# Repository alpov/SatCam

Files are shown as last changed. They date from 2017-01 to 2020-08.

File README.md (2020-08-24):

# PSAT-2 PSK/SSTV transponder

This repository hosts public parts of two boards from [PSAT2](http://www.aprs.org/psat2.html), a 1.5U CubeSat by US Naval Academy. These boards were developed at Dept. of Radio Electronics, Brno University of Technology, Czech Republic. The source files do not include authorization codes for SSTV and uplink commanding for PSK transponder.

**PSK transponder board** is an updated version of the PSK transponder with beacon and telemetry, used on [PSAT](http://www.aprs.org/psat.html) and [BRICSAT-1](http://www.aprs.org/bricsat-1.html). Transponder documentation available for [PSAT](http://www.urel.feec.vutbr.cz/esl/files/Projects/PSAT/P%20sat%20transponder%20WEB%20spec02.htm) and [BRICSAT-1](http://www.urel.feec.vutbr.cz/esl/files/Projects/BRICsat/Bricsat%20transponder%20WEB%20spec02.htm).

**SSTV transmitter board** provides a Slow-scan Television (SSTV) signal generator with PSK/CW telemetry, APRS uplink, and camera module. It is based on STM32F446RET6 microcontroller. Supported SSTV modes are Robot36, Robot72, MP73 and MP115.

## Important information (UPDATED Aug 2020)

* Current PSAT2 status
  * SSTV 70cm operational, images in Flash occasionally updated (thanks to PY5LF, OK2PNQ, OK5MP)
  * PSK 10m=>70cm transponder operational, mode A, open for users
  * APRS 2m is down (transmitter failure) => user SSTV commanding is not possible

* Please **send your SSTV images** to alpov@alpov.net. I am collecting the emails from reporters and occasionaly send them some news. Other info source is [AMSAT-BB](https://www.amsat.org/pipermail/amsat-bb/).
  * [Gallery of decoded SSTV images](http://www.urel.feec.vutbr.cz/esl/psat2/sstv/).
  * [Online telemetry decoder](http://www.urel.feec.vutbr.cz/esl/psat2/psat2tlm.php) - please use for PSK-31 telemetry upload.
  * [Decoded telemetry of PSK and SSTV boards](https://docs.google.com/spreadsheets/d/1X_4X0AgCshNDFIrDecOif41eRRwNzOKZwRn9tjI5_hs/edit?usp=sharing).
  * [SatNOGS for PSAT2](https://network.satnogs.org/observations/?future=0&good=1&bad=0&unvetted=0&failed=0&norad=44354).

* [Description of overlays](Docs/Overlay.md) in camera images.

* [Standalone camera design](Docs/SatCam.md) (for cancelled [PSAT3](http://www.aprs.org/psat3.html), [operations](Docs/PSAT3-operations.md)).

* [PocketQube camera design](Eagle/satcam_v4B_pocket_pcb_inside.pdf) (for [HADES](https://www.ure.es/camara-sstv-de-la-universidad-de-brno-para-el-satelite-hades-de-amsat-ea/) satellite).

## Transponder modes overview
The main function of the transponder is to receive PSK signals from 29.48 MHz uplink (passband from 29.4804 to 29.4826 MHz) and transmit them as a FM signal at 435.350 MHz downlink. The downlink is mixed with telemetry streams and SSTV images.

The PSK board switches between modes A to D according to available power. Battery voltage is checked periodically and after each transmitted character. If it crosses a boundary, the mode is switched. Moreover, if the voltage falls below a critical limit, the transmission is stopped immediately. This behavior can be observed in mode D, when only a part of the telemetry is transmitted.

All operations are limited to Sun detection, which is controlled by SUNWIRE signal. The SUNWIRE is fail-safe checked by state machine. After MCU reboot, the Sun signal is always high. It goes low after falling edge on SUNWIRE. If the SUNWIRE is low for more than 30 minutes, it is set to high automatically, otherwise with rising edge on SUNWIRE. Interconnects between both boards and PSAT-2 are shown [in a block diagram](Docs/psk_sstv_interconnect.png).

Communication is divided into 20sec time slots. There are 6 slots for modes A/B/C, and 9 slots for mode D. The telemetry is transmitted in every 1st slot or if PSK uplink is detected. Additionally, an SSTV image or telemetry is added to the transmitted signal. The time slots do not affect the PSK transponder function, so there is no need to fit with the PSK uplink signal into a time window. However, advanced functions such as commanding, telemetry and SSTV, are synchronized into these windows.

Users will be able to command these functions after the system has been successfully activated in space and we have completed successful checkout.

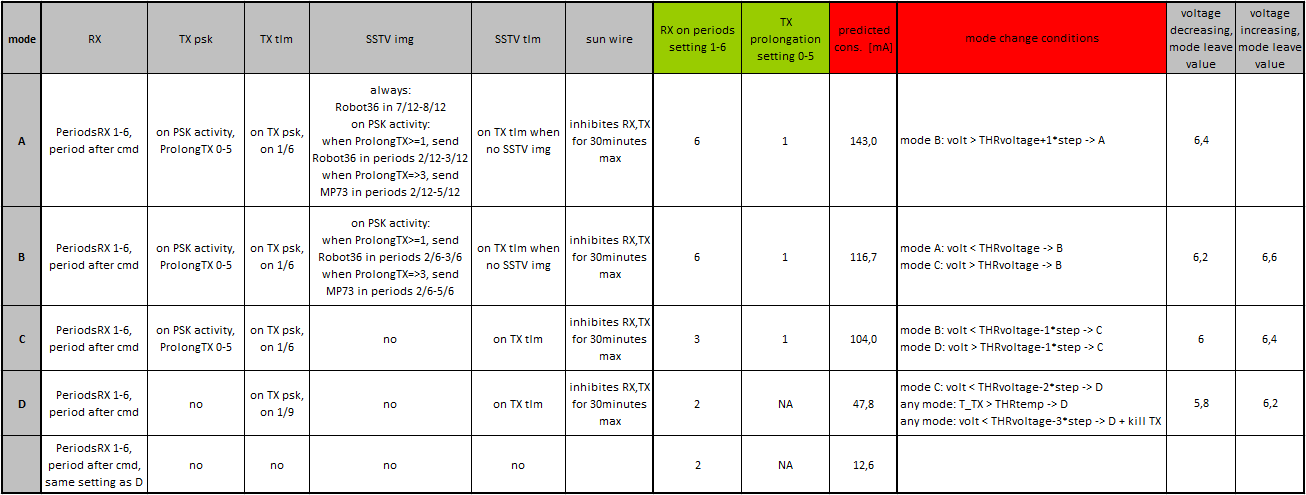
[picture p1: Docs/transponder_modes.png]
Transponder modes


## Telemetry streams
The PSK MCU generates telemetry data in PSK31 format, which is transmitted on 435.350 MHz, carrier at 374 Hz. This telemetry consists of current and historical frame. Current frame contains frame counter, reboot counter, values of PSK level, AGC, battery voltage, 5V voltage, current, RX temperature, and several period counter values. History frame is pseudo-randomly selected from memory and contains the same information except for period counters. Example telemetry frame: *PSAT-2 C apng eFaaijtkpokoaB aaaa A aokF eEadjluappjxay*. Such frame can be [decoded with the provided PHP decoder](http://www.urel.feec.vutbr.cz/esl/psat2/psat2tlm.php). Valid telemetry frames are automatically saved for further analysis.

The other telemetry stream is generated by SSTV MCU, transmitted in PSK31 format on the same frequency, carrier at 280 Hz. Telemetry contains current state of non-persistent tick counter, measurements of MCU temperature and ambient light in lux, state of several counters (authorization, planned events, reboots, errors, audio starts, camera images, commands accepted, commands rejected, commands unauthorized). Example telemetry frame: *PSAT-2 S ashd aDbiaaaa qralaitkboFxaa*. Again, such frame can be [decoded with the provided PHP decoder](http://www.urel.feec.vutbr.cz/esl/psat2/psat2tlm.php).

## SSTV operation
SSTV MCU can be commanded through APRS commands. If no command is received during 60 seconds, it starts *auto* mode. In this mode, all transmissions are synchronized to PSK TX. SSTV board can transmit PSK telemetry or SSTV images in Robot36 and MP73 modes. Images are progressively selected alternately from ROM and FLASH. ROM images are hard-coded to firmware, while FLASH images are grabbed from on-board camera. After each reboot, first 8 images in FLASH are taken with 30sec separation.

APRS commands addressed to special callsign will change the mode to *manual*. Details on public commanding will be added after successful deployment and initial testing of the satellite.

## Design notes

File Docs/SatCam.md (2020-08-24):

# SatCam - SSTV encoder for OV2640

SatCam in an SSTV encoder with OV2640 camera. It is based on STM32F446RET6 microcontroller. Supported SSTV modes are Robot36, Robot72, MP73 and MP115. SatCam was originally developed as a part of PSAT2 satellite project and later redesigned as a stand-alone module.

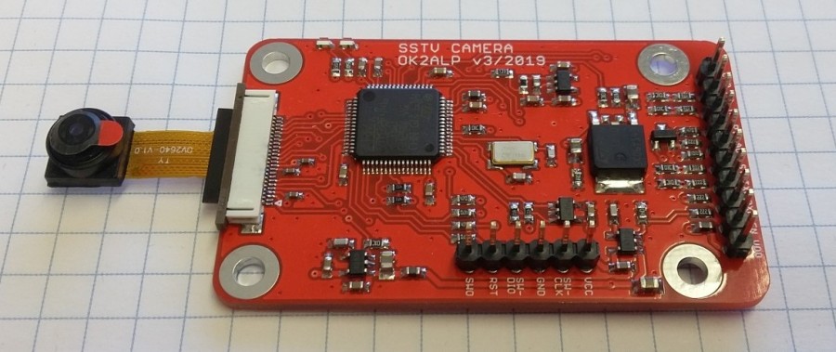
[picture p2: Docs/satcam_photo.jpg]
SatCam prototype photo


[SatCam schematic](../Eagle/satcam_v3_mini_sch.pdf) - [SatCam PCB](../Eagle/satcam_v3_mini_tvalues.pdf)

SatCam can be commanded from e.g. an APRS link, the UART works at 9600 8N1. It looks for `SATCAMERA:` keyword, followed by a command, case insensitive. End of line is `<CR>`, `<LF>` or `{`. Empty lines and messages without proper keyword are ignored. All commands including the keyword are case insensitive. Example: `SatCamera:sstv.live.73<CR>`.

Another way of using SatCam is to setup its initial configuration with UART and then use its input signals only.

## Pin connections
| Pin | Description |
| ----- | --- |
| `M0`  | mode select (0-3)
| `M1`  | mode select (0-3)
| `PTT` | open-drain PTT output, active low during TX
| `AUD` | audio output
| `ST`  | start trigger input
| `RXD` | UART input
| `TXD` | UART output
| `EN`  | voltage regulator enable input
| `VDD` | power supply

Silkscreen of `RXD` and `TXD` is mixed up on the 1st PCB revision. Current schematic and PCB use the ordinary meaning (RXD is the input to SatCam, TXD it the output).

## Voltage levels
| Pin | Levels |
| ----- | --- |
| `ST`, `M0`, `M1`  | 5V (can be changed with R7, R8, R9)
| `TXD`, `RXD` | 3V3 (RXD can be changed with R4, TXD needs level converter)
| `EN` | >2.3V enabled, <0.5V or open disabled
| `PTT` | open-drain, max. 25V
| `AUD` | default SSTV audio is 1.5Vpp to high impedance (>5kohm) load
| `VDD` | 3.2-16V (3.1-6V if R31=0ohm, IC6 not placed)

## Current consumption
| Mode | Avg. current |
| --- | --- |
| disabled with EN input | 0.6mA
| idle, monitoring UART | 2.8mA
| taking picture, ~1.3 seconds before each image | 60.6mA
| transmitting audio, with short peaks | 10.3mA

## Tested OV2640 modules
* [AdvancedTech](https://www.aliexpress.com/item/32898143505.html): landscape, FOV ~50°, [example](ov2640_AdvancedTech.jpg)
* [Your Cee Mini](https://www.aliexpress.com/item/33058626691.html): landscape, FOV ~60°, [example](ov2640_YourCeeMini.jpg)
* [Your Cee Wide](https://www.aliexpress.com/item/33058626691.html): landscape, FOV ~120°, [example](ov2640_YourCeeWide.jpg)
* [Alice1101983](https://www.aliexpress.com/item/32978120017.html), [ModuleFans](https://www.aliexpress.com/item/33042725935.html): portrait, [example](ov2640_Alice.jpg)

## SatCam commands

The module monitors RXD line when idle and looks for `SATCAMERA:` identifier. Expected commands are for SSTV, PSK and CW systems. Other commands (CAMCFG and DEBUG) are protected by a PIN. User PIN can be set to a custom number, master PIN is fixed for the particular module (computed from the MCU unique ID). It is possible to send protected commands for the next 15 minutes after the AUTH command with a correct PIN. Master PIN can be read using `psk.nvinfo` and `debug.status` commands in case when the user PIN is not set (i.e. is zero).

| Command syntax | Example | Parameters |
| --- | --- | --- |
| `sstv.live.MODE.OVERLAY` | `sstv.live.36` (send picture as Robot36) | MODE is `36` for Robot36, `72` for Robot72, `73` for MP73, `115` for MP115 (default: 36)
| `sstv.rom.MODE.PAGE_NUMBER.OVERLAY` | `sstv.rom.115.3.hello` (send hardcoded image 3 as MP115, with overlay) | PAGE_NUMBER is ROM memory page (default: 0), OVERLAY is user-defined text, `.` and `{` not allowed, up to 13 chars (default: none)
| `psk.MESSAGE.SPEED.FREQ` | `psk.hello.31.1000` (send message as PSK-31 at 1kHz) | MESSAGE is either user-defined text (`.` and `{` not allowed) or `nvinfo` or `config`
| `psk.config.SPEED.FREQ` | `psk.config.125.1000` (send configuration as PSK-125 at 1kHz) | SPEED is `31`, `63`, `125`, `250`, `500`, `1000` (default: 31, for config/nvinfo: 125)
| `psk.nvinfo.SPEED.FREQ` | `psk.nvinfo.125.1000` (send NVinfo log as PSK-125 at 1kHz) | FREQ is 100-7000Hz (default: 800)
| `cw.MESSAGE.WPM.FREQ` | `cw.hello.25.1000` (send message as 25WPM CW at 1kHz) | WPM is word per minute speed (5 to 40)
| `auth.PIN` | `auth.1234` (authorize with PIN 1234) | PIN is user or master access code

| Command syntax | Default | Description |
| --- | --- | --- |
| `camcfg.delay.DELAY` | 1000 | Camera module initial delay. DELAY is 100-5000ms.
| `camcfg.qs.QS` | 5 | JPEG quality factor. QS is 0-255.
| `camcfg.agc.ceiling.AGC_CEILING` | 16 | Automatic gain control. AGC_CEILING is 2, 4, 8, 16, 32, 64, 128.
| `camcfg.agc.manual.AGC_VALUE` | 0 | Manual gain control. AGC_MANUAL is 0-1023.
| `camcfg.aec.auto` | | Automatic exposure control.
| `camcfg.aec.manual.AEC_VALUE` | `auto` | Manual exposure time. AEC is 0-65535 or `auto`.
| `camcfg.awb.AWB_TYPE` | `sunny` | Automatic white balabce. AWB is `auto`, `sunny`, `cloudy`, `office`, `home`.
| `camcfg.rotate.ROTATE` | off | Camera rotation (upside down). ROTATE is `off` or `on`.
| `camcfg.start.0.COMMAND` | `SSTV.LIVE.36` | Command for M0=0, M1=0.
| `camcfg.start.1.COMMAND` | `SSTV.LIVE.73` | Command for M0=1, M1=0.
| `camcfg.start.2.COMMAND` | `PSK.NVINFO.125.1000` | Command for M0=0, M1=1.
| `camcfg.start.3.COMMAND` | `SSTV.ROM.115.0` | Command for M0=1, M1=1.
| `camcfg.startedge.EDGE_VALUE` | `any` | Active edge for ST trigger input. EDGE_VALUE is `none`, `rising`, `falling` or `any`.
| `camcfg.holdoff.HOLDOFF_TIME` | 2 | Hold-off time after command before next edge detection start. HOLDOFF_TIME is 0-65535sec.
| `camcfg.callsign.CALLSIGN` | `SatCam` | Module callsign, for SSTV overlay and PSK/CW messages.
| `camcfg.autoreboot.REBOOT_TIME` | 0 | Periodic reboot. REBOOT_TIME is 0 or >=120sec. Careful when uptime>autoreboot, camera will reboot immediately without saving the value.
| `camcfg.userpin.PIN` | 0 | Set user PIN for `camcfg` and `debug` commands.
| `camcfg.clearlog` | | Clear EEPROM logs.
| `camcfg.reboot` | | Safe MCU reboot (with NVIC).
| `camcfg.load` | | Load configuration from EEPROM (always after power-up).
| `camcfg.save` | | Save current configuration to EEPROM.
| `camcfg.default` | | Load default SatCam configuration.

| Command syntax | Description |
| --- | --- |
| `debug.status` | Write status (configuration and NVinfo) to terminal.
| `debug.reset.RESET_TYPE` | Debug MCU reset. RESET_TYPE is `nvic`, `watchdog`, `fault`.
| `debug.sendjpeg` | Send JPEG from camera to terminal.
| `debug.eeprom.fullerase` | Perform full EEPROM erase (configuration and logs).
| `debug.eeprom.dump` | Dump configuration EEPROM page to terminal.
| `debug.adc.voltage` | Measure VDD voltage and write to terminal.
| `debug.adc.temp` | Measure core temperature and write to terminal.

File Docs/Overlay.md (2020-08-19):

## Live image from camera
`PSAT-2 +69605 8°C #062 89lx1`
* `+69605` timestamp - minutes elapsed since reboot
* `8°C` MCU temperature when taking the image
* `#062` counter of camera snapshots
* `89lx1` light when taking the image, mantisa and exponent in lux, i.e. 89*10^1 = 890lux
* Timestamp, temperature and light are actual.
* Note: Light exposition seems to be too low - sensor was probably misplaced during satellite integration.

## Image from Flash memory
`PSAT-2 +24940 11°C #047 17lx3 F#13`
* Timestamp, temperature and light are from the moment of shooting.
* `F#13` is position no. 13

## Image from ROM memory
`PSAT-2 +26148 16°C ROM #10`
* Timestamp and temperature are actual.
* `ROM #10` is position no. 10.

## Thumbnail image from all Flash memories
`PSAT-2 +29312 13°C thumbnails`
* Timestamp and temperature are actual.

## Camera information
`11520B g256 e9`
* `11520B` - size of original JPEG snapshot
* `g256` - camera gain (AGC)
* `e9` - camera exposure (AEC)

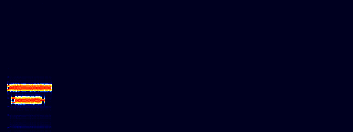
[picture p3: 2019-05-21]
Docs/modeC_no_PSK.PNG

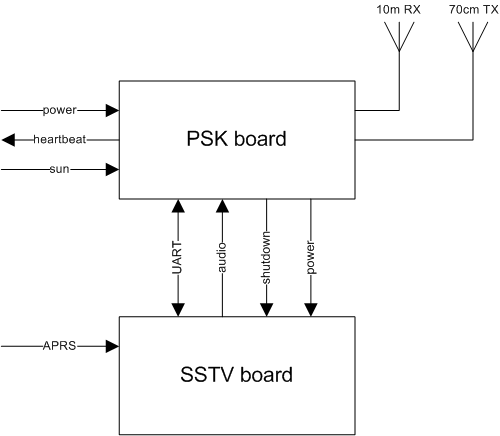
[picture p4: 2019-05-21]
Docs/psk_sstv_interconnect.png

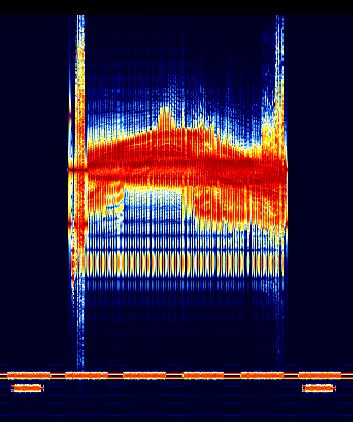
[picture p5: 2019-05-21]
Docs/modeB_with_PSK_TXprolong3.PNG

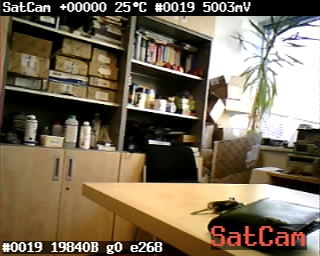
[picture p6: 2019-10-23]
Docs/ov2640_YourCeeMini.jpg

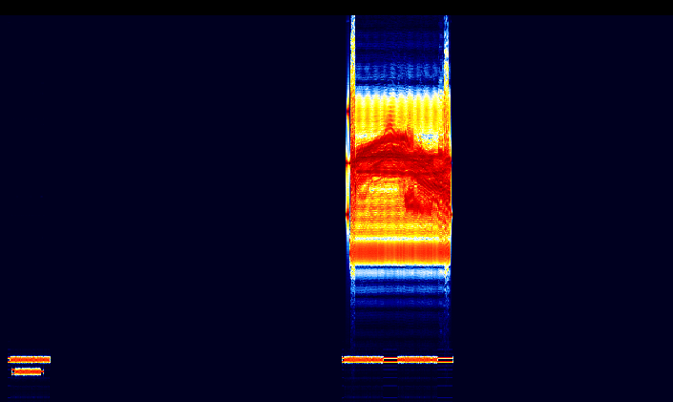
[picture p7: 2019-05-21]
Docs/modeA_no_PSK.PNG

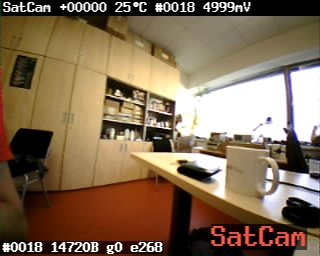
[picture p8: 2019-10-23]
Docs/ov2640_YourCeeWide.jpg

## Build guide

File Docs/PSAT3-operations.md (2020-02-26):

# SSTV camera on PSAT3

SatCam is an [SSTV encoder with OV2640 camera](SatCam.md). It is based on STM32F446RET6 microcontroller. Supported SSTV modes are Robot36, Robot72, MP73 and MP115. SatCam was originally developed as a part of PSAT2 satellite project and later redesigned as a stand-alone module.

When enabled, camera **sends a live picture** in Robot36 or MP73 **every 10 minutes**. The SSTV transmission always come after APRS.

## Current status

* Current PSAT3 status: **waiting for deploy**

* Gallery of SSTV images - TBD. SatNOGS for PSAT3 - TBD. Please send your SSTV images and received runtime status (NVinfo) to alpov@alpov.net.

## SatCam commanding

SatCam can be commanded from the APRS link. It looks for `SATCAMERA:` keyword, followed by a command, case insensitive. Every HAM is allowed to use the following camera commands when the system is enabled.

| Command syntax | Parameters |
| --- | --- |
| `satcamera:sstv.live.MODE.OVERLAY` | MODE is `36` for Robot36, `72` for Robot72, `73` for MP73, `115` for MP115 (default: 36), OVERLAY is user-defined text, `.` and `{` not allowed, up to 13 chars (default: none)
| `satcamera:psk.MESSAGE.SPEED.FREQ` | MESSAGE is either user-defined text (`.` and `{` not allowed) or `nvinfo` or `config`, SPEED is `31`, `63`, `125`, `250`, `500`, `1000` (default: 31, for config/nvinfo: 125), FREQ is 100-7000Hz (default: 800)
| `satcamera:cw.MESSAGE.WPM.FREQ` | MESSAGE is either user-defined text (`.` and `{` not allowed), WPM is word per minute speed (5 to 40), FREQ is 100-7000Hz (default: 800)

| Command examples | Description |
| --- | --- |
| `satcamera:sstv.live` | Send live picture in Robot36
| `satcamera:sstv.live.73` | Send live picture in MP73
| `satcamera:sstv.live.115.de OK2ALP` | Send live picture in MP115, add overlay to image
| `satcamera:psk.hello from space` | Send message `PSAT3 hello from space` in PSK-31 at 800Hz carrier
| `satcamera:psk.config` | Send camera configuration in PSK-125 @ 800Hz
| `satcamera:psk.nvinfo` | Send camera runtime status in PSK-125 @ 800Hz
| `satcamera:cw` | Send a welcome message `73 DE PSAT3 PSAT3 PSAT3 K` at 25WPM @ 800Hz
| `satcamera:cw.morse forever.18` | Send message `PSAT3 morse forever` at 18WPM @ 800Hz

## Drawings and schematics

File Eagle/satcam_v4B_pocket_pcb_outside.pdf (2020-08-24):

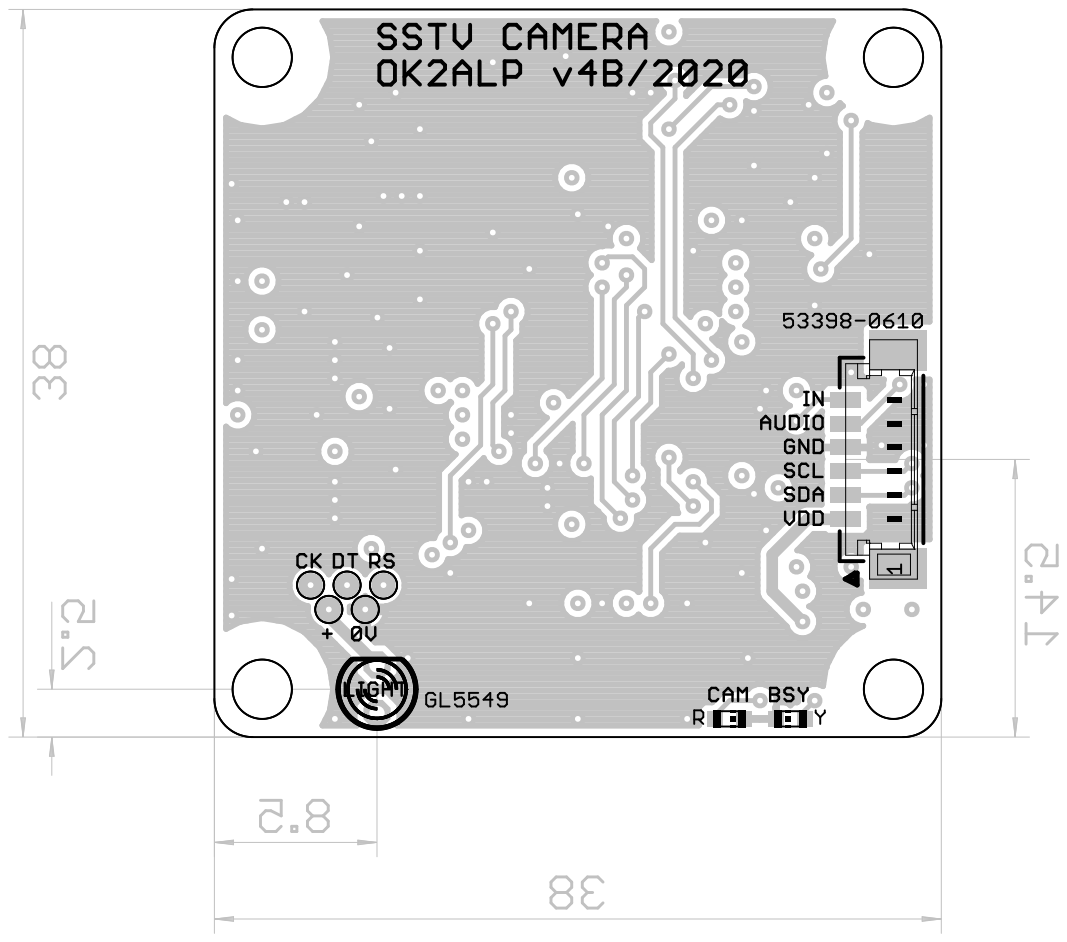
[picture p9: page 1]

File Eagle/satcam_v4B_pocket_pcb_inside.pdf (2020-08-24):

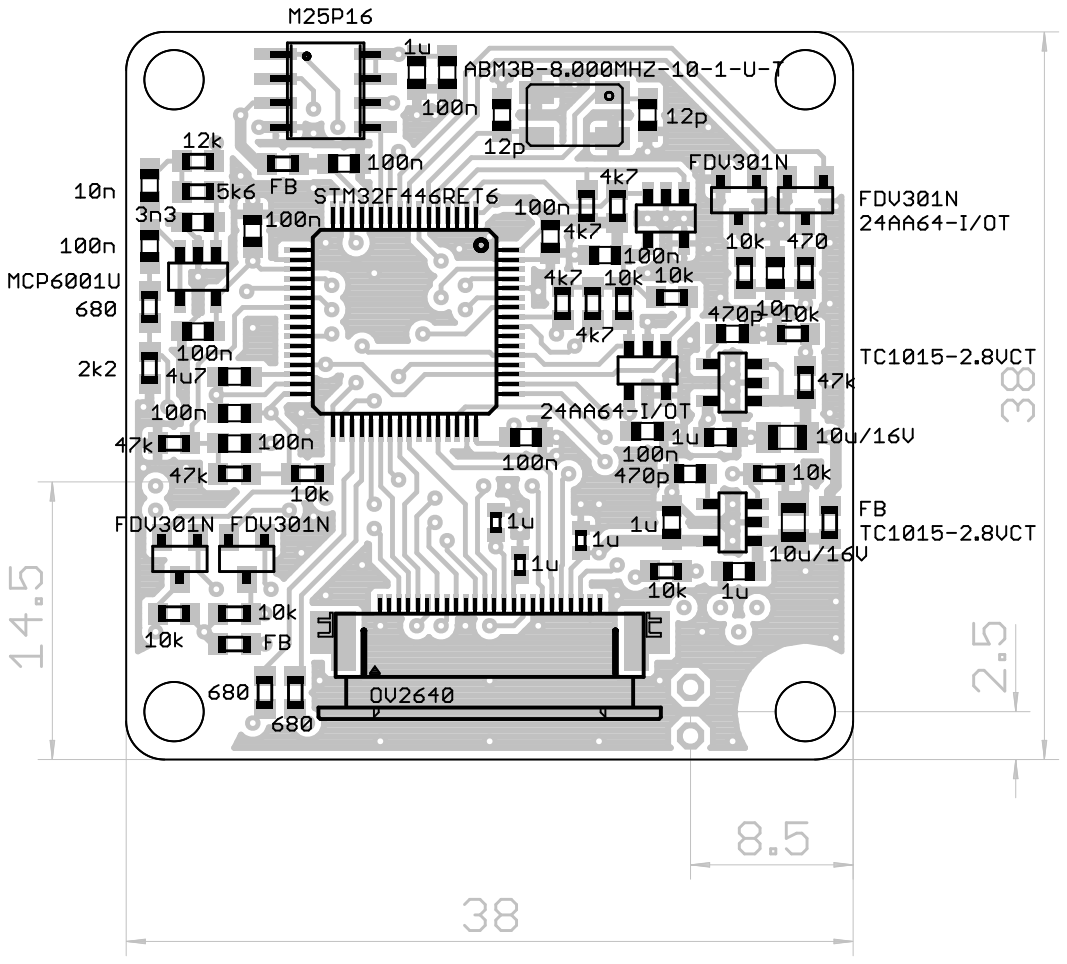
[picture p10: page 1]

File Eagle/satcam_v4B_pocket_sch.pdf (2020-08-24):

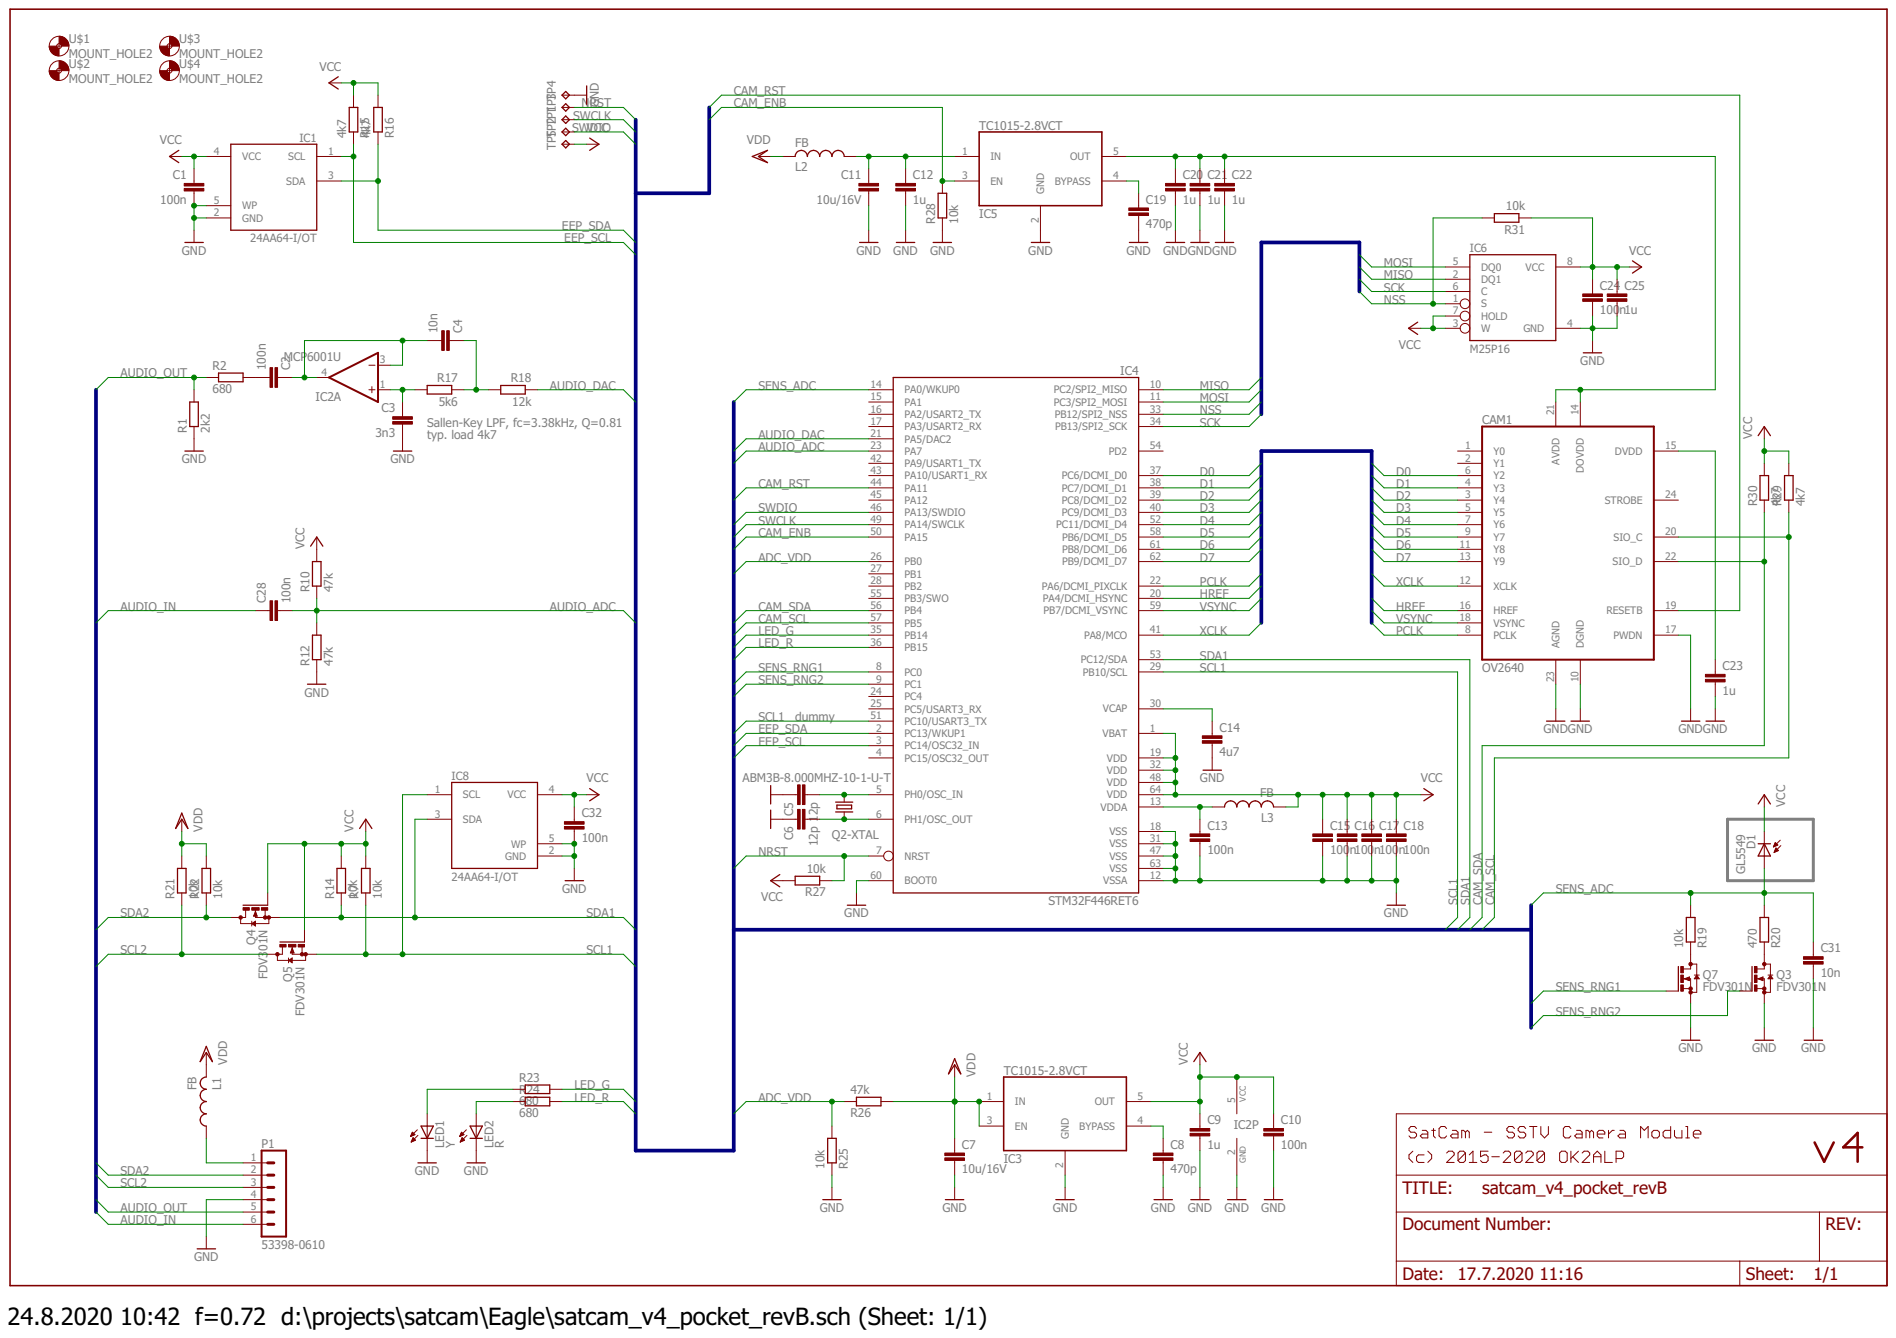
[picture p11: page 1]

Sallen-Key LPF, fc=3.38kHz, Q=0.81
typ. load 4k7

20 SIO_D

22 RESETB

REV: TITLE: Document Number: satcam_v4_pocket_revB

Date: 17.7.2020 11:16 | Sheet: 1/1

24.8.2020 10:42 f=0.72 d:\projects\satcam\Eagle\satcam_v4_pocket_revB.sch (Sheet: 1/1)

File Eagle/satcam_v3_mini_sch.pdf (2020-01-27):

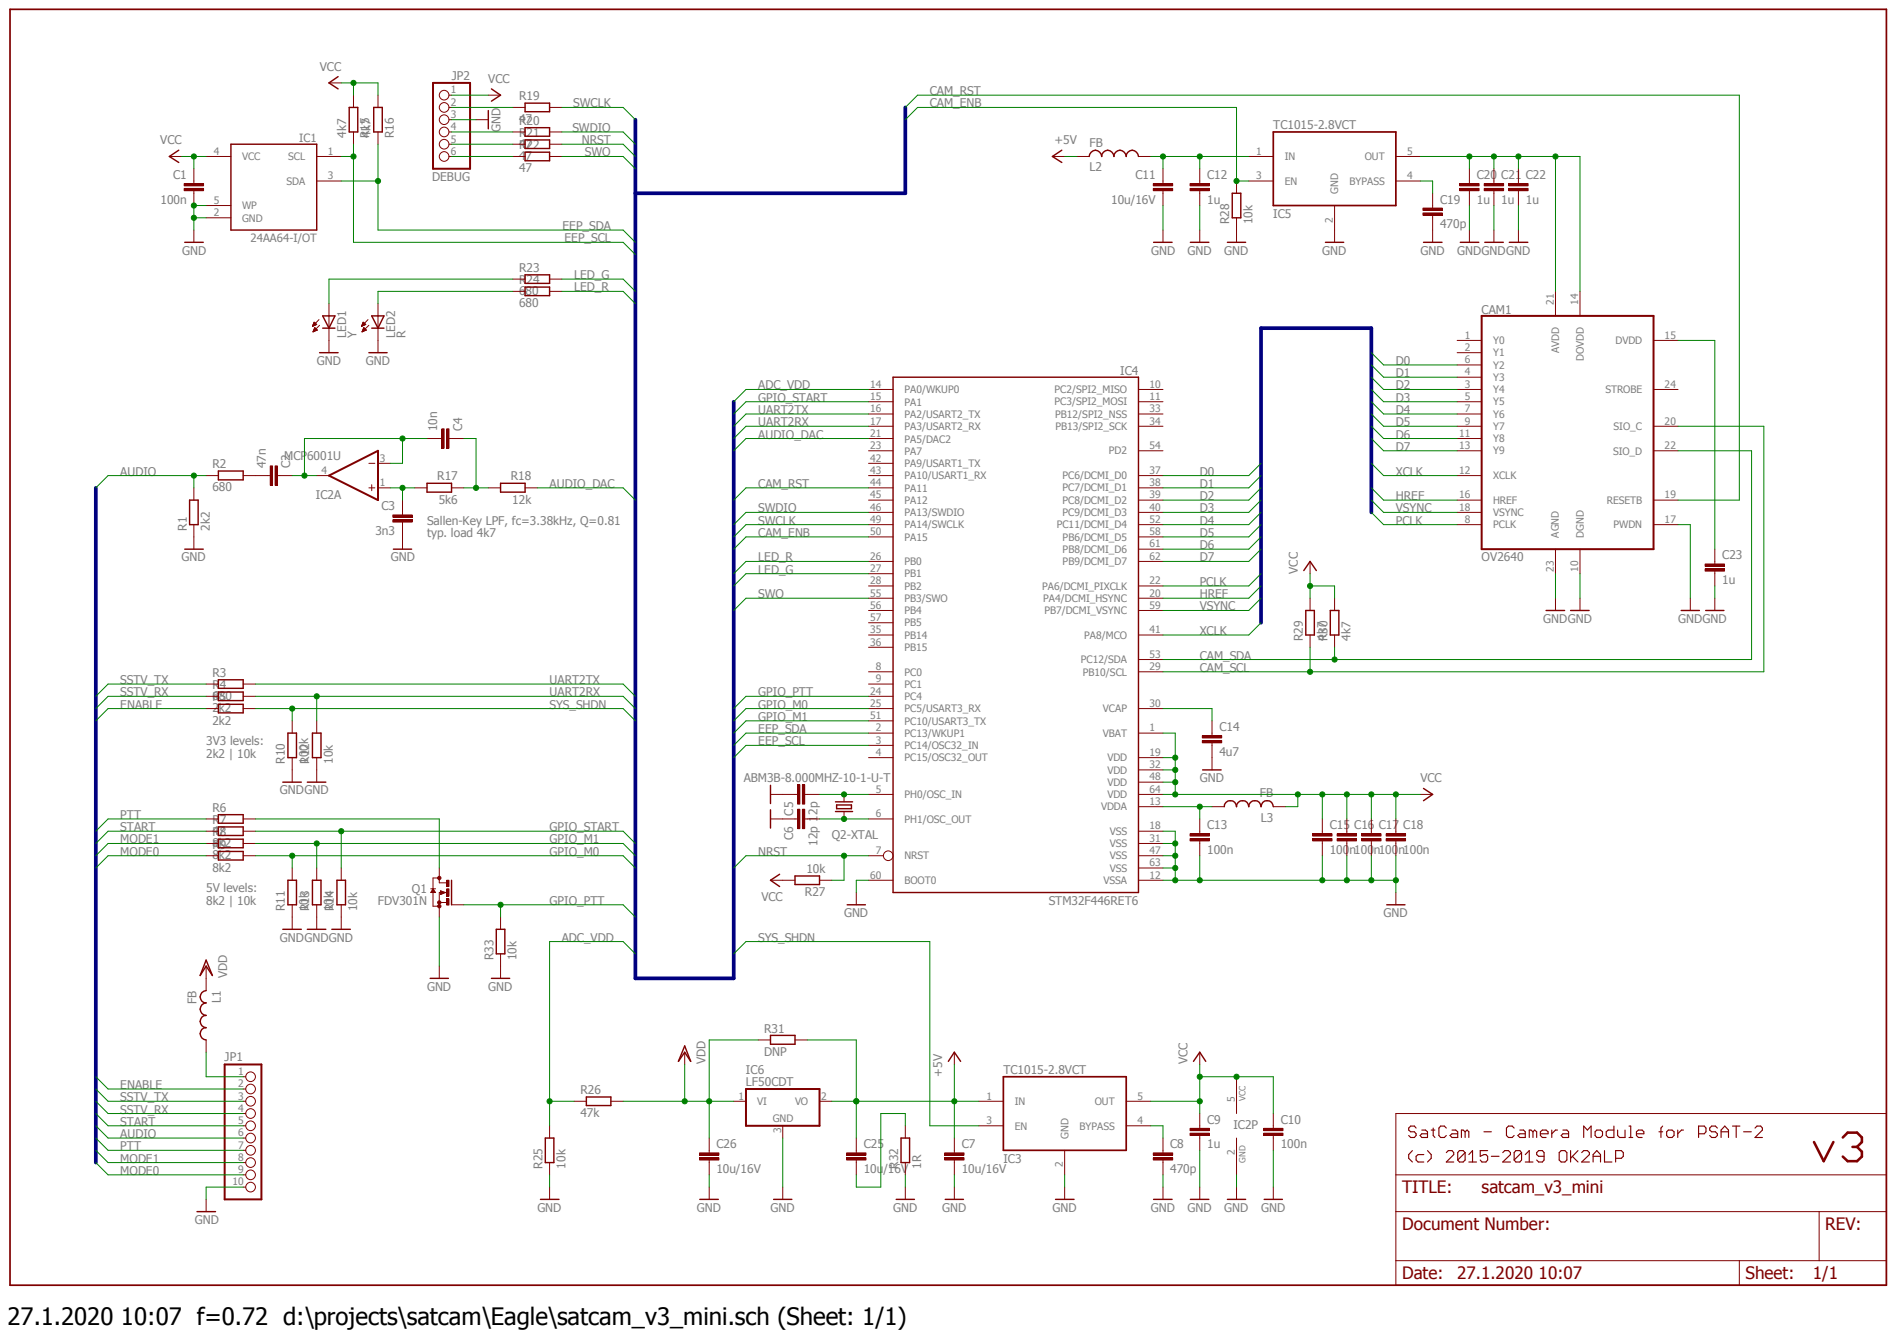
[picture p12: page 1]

Sallen-Key LPF, fc=3.38kHz, Q=0.81
typ. load 4k7

Document Number: | REV:

Date: 27.1.2020 10:07 | Sheet: 1/1

27.1.2020 10:07 f=0.72 d:\projects\satcam\Eagle\satcam_v3_mini.sch (Sheet: 1/1)

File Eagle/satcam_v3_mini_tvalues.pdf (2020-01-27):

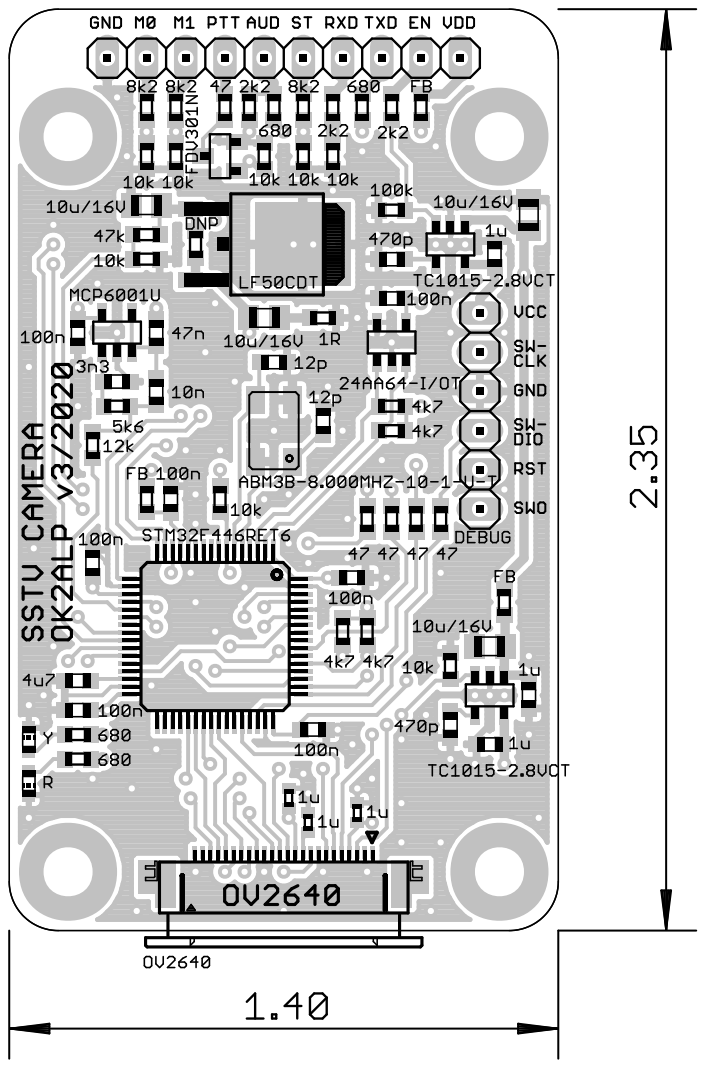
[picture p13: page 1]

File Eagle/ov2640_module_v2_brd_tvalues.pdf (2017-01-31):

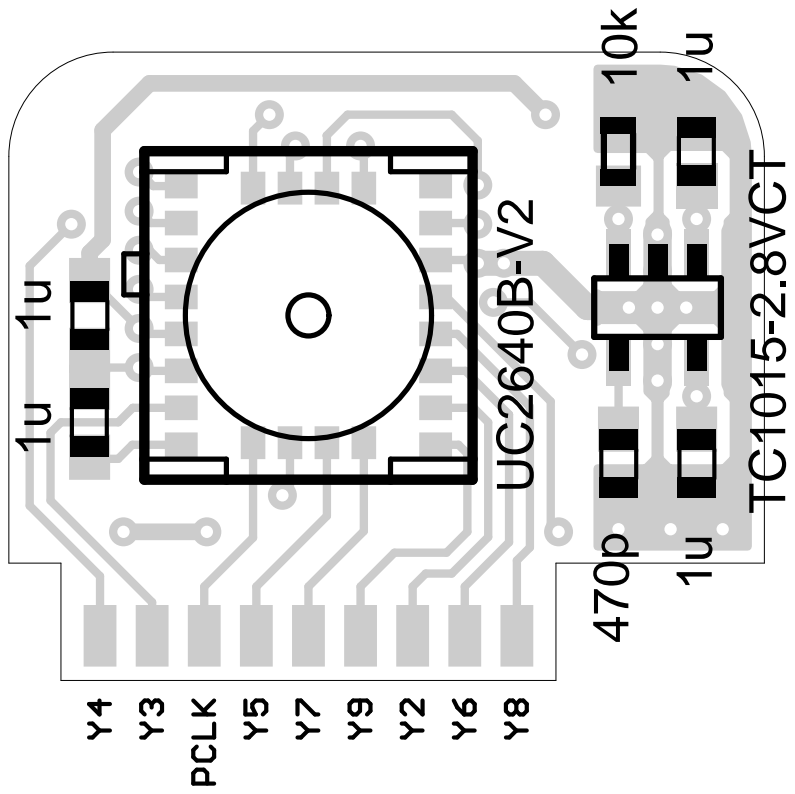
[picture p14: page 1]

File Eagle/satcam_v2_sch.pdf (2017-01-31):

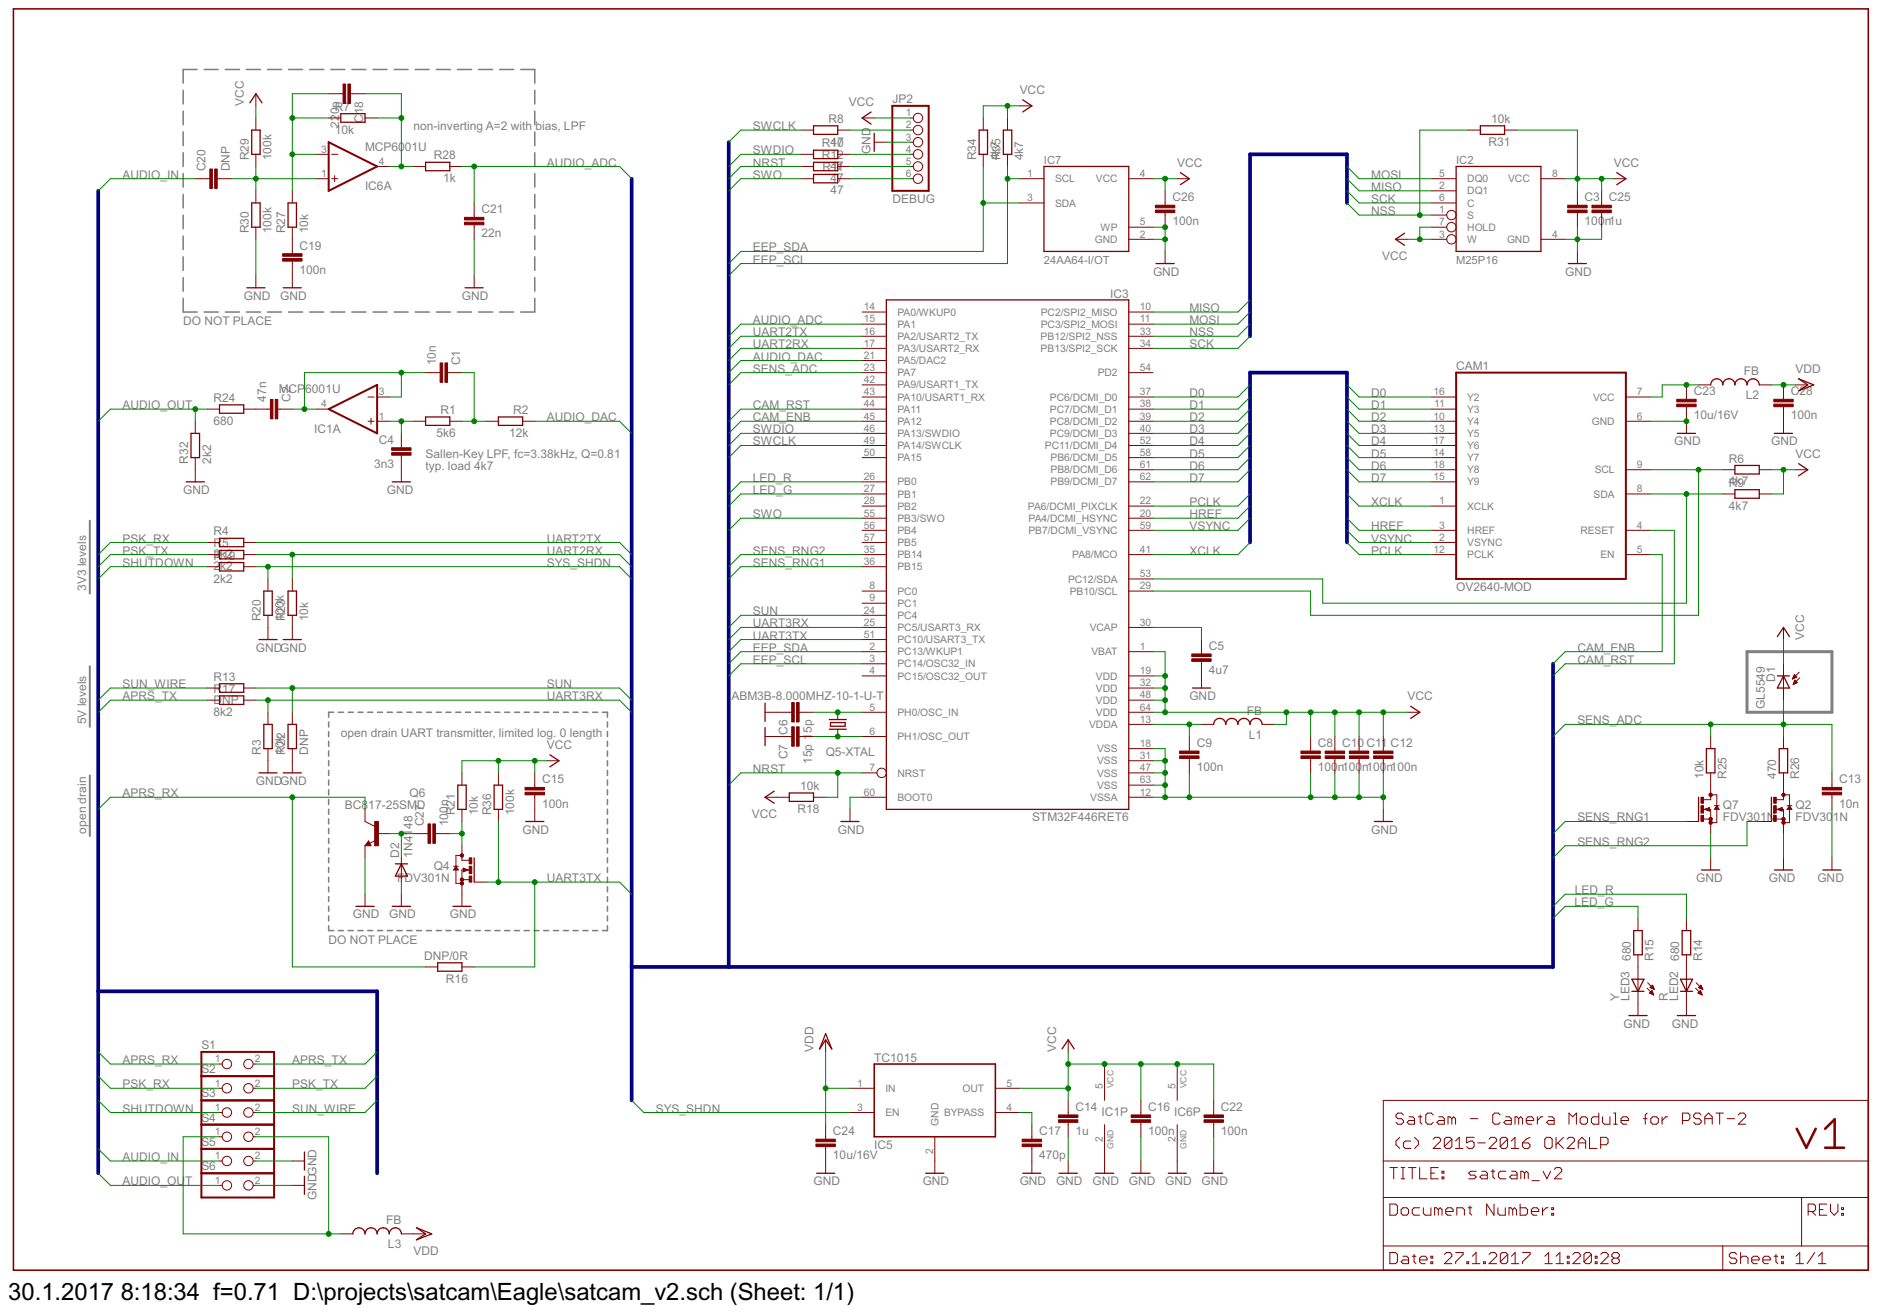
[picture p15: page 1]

non-inverting A=2 with bias, LPF

Sallen-Key LPF, fc=3.38kHz, Q=0.81
typ. load 4k7

30.1.2017 8:18:34 f=0.71 D:\projects\satcam\Eagle\satcam_v2.sch (Sheet: 1/1)

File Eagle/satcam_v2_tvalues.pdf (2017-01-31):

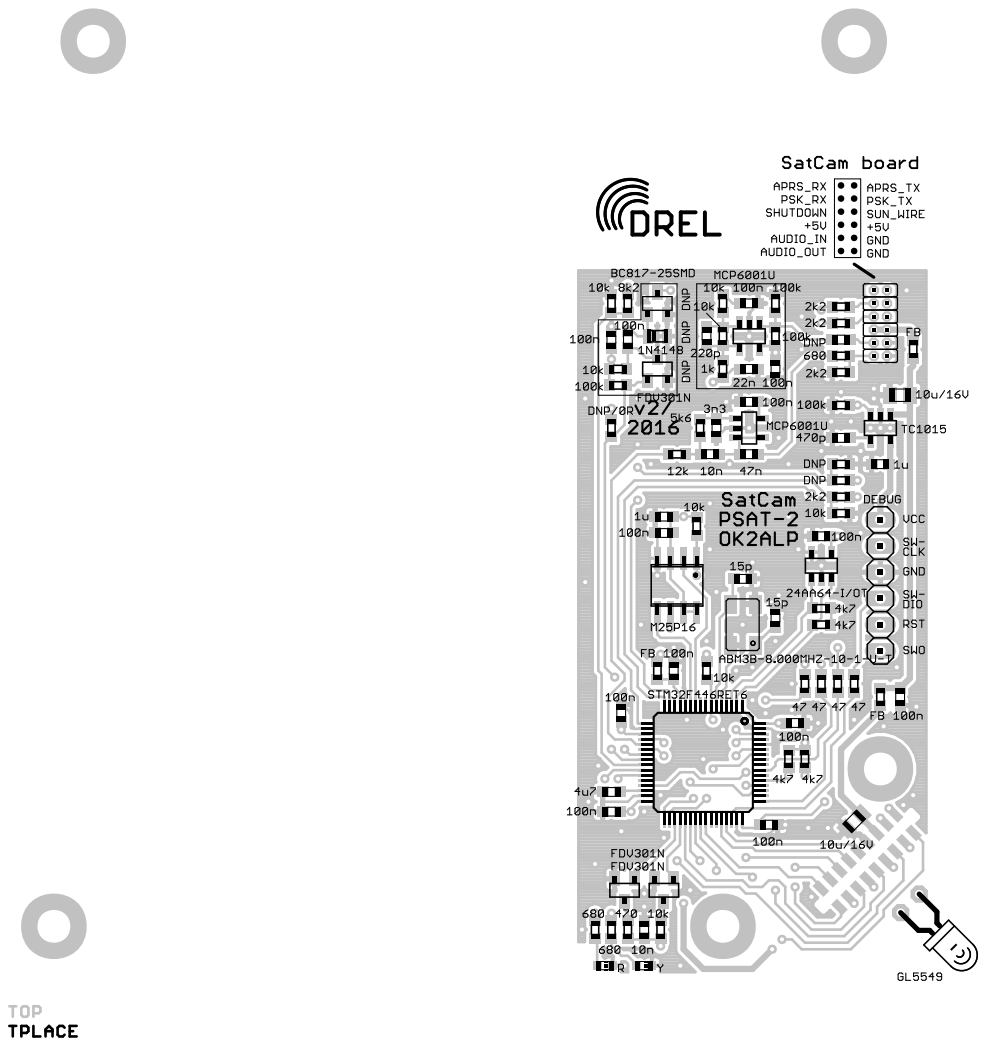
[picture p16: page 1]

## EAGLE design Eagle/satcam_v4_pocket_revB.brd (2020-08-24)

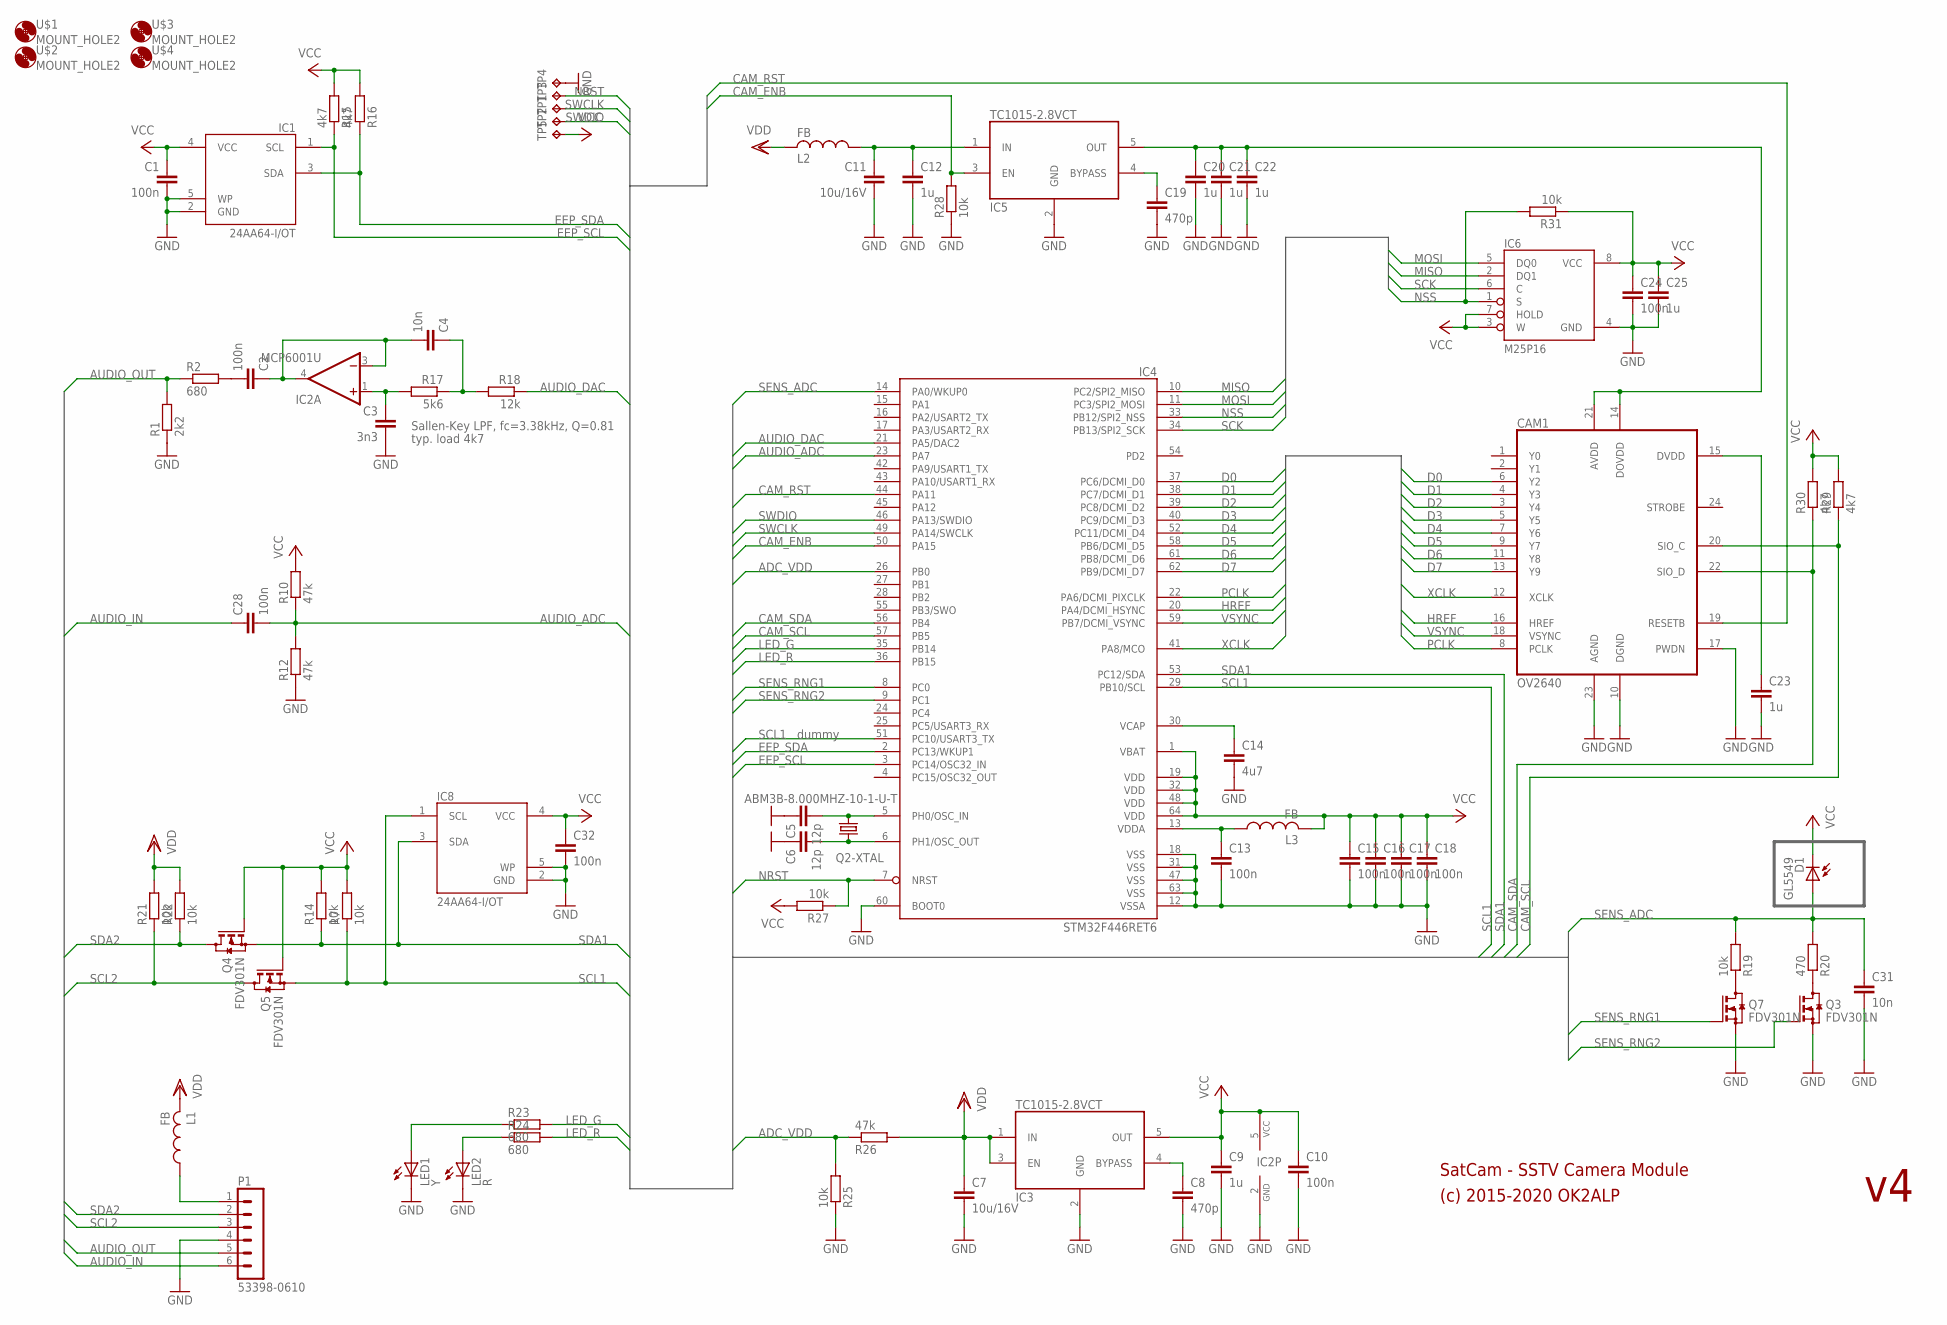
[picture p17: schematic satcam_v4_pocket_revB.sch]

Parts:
C1, C2, C10, C13, C15, C16, C17, C18, C24, C28, C32: 100n; C0603
C3: 3n3; C0603
C4, C31: 10n; C0603
C5, C6: 12p; C0603
C7, C11: 10u/16V; C0805K
C8, C19: 470p; C0603
C9, C12, C20, C25: 1u; C0603
C14: 4u7; C0603
C21, C22, C23: 1u; C0402
CAM1: OV2640; 52745-2490
D1: GL5549; LED3MM
IC1, IC8: 24AA64-I/OT; SOT23-5
IC2: MCP6001U; SOT23-5
IC3, IC5: TC1015-2.8VCT; SOT23-5
IC4: STM32F446RET6; TQFP64-10X10
IC6: M25P16; SO08
L1, L2, L3: FB; R0603
LED1: Y; CHIP-LED0603
LED2: R; CHIP-LED0603
P1: 53398-0610
Q2: ABM3B-8.000MHZ-10-1-U-T; CER5032
Q3, Q4, Q5, Q7: FDV301N; SOT23
R1: 2k2; R0603
R2, R23, R24: 680; R0603
R7, R14, R19, R21, R22, R25, R27, R28, R31: 10k; R0603
R10, R12, R26: 47k; R0603
R15, R16, R29, R30: 4k7; R0603
R17: 5k6; R0603
R18: 12k; R0603
R20: 470; R0603
TP1, TP2, TP3, TP4, TP5: TPB1,27; B1,27
U$1, U$2, U$3, U$4: MOUNT_HOLE2; 3,2

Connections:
ADC_VDD: IC4.26 (PB0), R25.2, R26.1
AUDIO_ADC: C28.2, IC4.23 (PA7), R10.1, R12.2
AUDIO_DAC: IC4.21 (PA5/DAC2), R18.1
AUDIO_IN: C28.1, P1.6
AUDIO_OUT: P1.5, R1.2, R2.1
CAM_ENB: IC4.50 (PA15), IC5.3 (EN), R28.2
CAM_RST: CAM1.19 (RESETB), IC4.44 (PA11)
CAM_SCL: CAM1.20 (SIO_C), IC4.57 (PB5), R29.1
CAM_SDA: CAM1.22 (SIO_D), IC4.56 (PB4), R30.1
D0: CAM1.6 (Y2), IC4.37 (PC6/DCMI_D0)
D1: CAM1.4 (Y3), IC4.38 (PC7/DCMI_D1)
D2: CAM1.3 (Y4), IC4.39 (PC8/DCMI_D2)
D3: CAM1.5 (Y5), IC4.40 (PC9/DCMI_D3)
D4: CAM1.7 (Y6), IC4.52 (PC11/DCMI_D4)
D5: CAM1.9 (Y7), IC4.58 (PB6/DCMI_D5)
D6: CAM1.11 (Y8), IC4.61 (PB8/DCMI_D6)
D7: CAM1.13 (Y9), IC4.62 (PB9/DCMI_D7)
EEP_SCL: IC1.1 (SCL), IC4.3 (PC14/OSC32_IN), R15.1
EEP_SDA: IC1.3 (SDA), IC4.2 (PC13/WKUP1), R16.1
GND: C1.2, C3.2, C5.1, C6.1, C7.2, C8.2, C9.2, C10.2, C11.2, C12.2, C13.2, C14.2, C15.2, C16.2, C17.2, C18.2, C19.2, C20.2, C21.2, C22.2, C23.2, C24.2, C25.2, C31.2, C32.2, CAM1.10 (DGND), CAM1.17 (PWDN), CAM1.23 (AGND), IC1.2 (GND), IC1.5 (WP), IC2.2 (GND), IC3.2 (GND), IC4.12 (VSSA), IC4.18 (VSS), IC4.31 (VSS), IC4.47 (VSS), IC4.60 (BOOT0), IC4.63 (VSS), IC5.2 (GND), IC6.4 (GND), IC8.2 (GND), IC8.5 (WP), LED1.C, LED2.C, P1.4, Q2.2 (GND), Q2.4 (GND), Q3.2 (S), Q7.2 (S), R1.1, R12.1, R25.1, R28.1, TP4.TP
HREF: CAM1.16 (HREF), IC4.20 (PA4/DCMI_HSYNC)
LED_G: IC4.35 (PB14), R23.2
LED_R: IC4.36 (PB15), R24.2
MISO: IC4.10 (PC2/SPI2_MISO), IC6.2 (DQ1)
MOSI: IC4.11 (PC3/SPI2_MOSI), IC6.5 (DQ0)
unnamed: C11.1, C12.1, IC5.1 (IN), L2.1
unnamed: C23.1, CAM1.15 (DVDD)
unnamed: C19.1, IC5.4 (BYPASS)
unnamed: L1.1, P1.1
unnamed: C8.1, IC3.4 (BYPASS)
unnamed: LED2.A, R24.1
unnamed: LED1.A, R23.1
unnamed: C14.1, IC4.30 (VCAP)
unnamed: Q7.3 (D), R19.1
unnamed: Q3.3 (D), R20.1
unnamed: C13.1, IC4.13 (VDDA), L3.1
unnamed: C6.2, IC4.6 (PH1/OSC_OUT), Q2.3 (2)
unnamed: C5.2, IC4.5 (PH0/OSC_IN), Q2.1
unnamed: C2.1, C4.2, IC2.3 (-IN), IC2.4 (OUT)
unnamed: C4.1, R17.1, R18.2
unnamed: C3.1, IC2.1 (+IN), R17.2
unnamed: C2.2, R2.2
NRST: IC4.7 (NRST), R27.1, TP3.TP
NSS: IC4.33 (PB12/SPI2_NSS), IC6.1 (S), R31.2
PCLK: CAM1.8 (PCLK), IC4.22 (PA6/DCMI_PIXCLK)
SCK: IC4.34 (PB13/SPI2_SCK), IC6.6 (C)
SCL1: IC4.29 (PB10/SCL), IC4.51 (PC10/USART3_TX), IC8.1 (SCL), Q5.2 (S), R7.1
SCL2: P1.3, Q5.3 (D), R21.1
SDA1: IC4.53 (PC12/SDA), IC8.3 (SDA), Q4.2 (S), R14.1
SDA2: P1.2, Q4.3 (D), R22.1
SENS_ADC: C31.1, D1.A, IC4.14 (PA0/WKUP0), R19.2, R20.2
SENS_RNG1: IC4.8 (PC0), Q7.1 (G)
SENS_RNG2: IC4.9 (PC1), Q3.1 (G)
SWCLK: IC4.49 (PA14/SWCLK), TP1.TP
SWDIO: IC4.46 (PA13/SWDIO), TP2.TP
VCAM: C20.1, C21.1, C22.1, CAM1.14 (DOVDD), CAM1.21 (AVDD), IC5.5 (OUT)
VCC: C1.1, C9.1, C10.1, C15.1, C16.1, C17.1, C18.1, C24.1, C25.1, C32.1, D1.K (C), IC1.4 (VCC), IC2.5 (VCC), IC3.5 (OUT), IC4.1 (VBAT), IC4.19 (VDD), IC4.32 (VDD), IC4.48 (VDD), IC4.64 (VDD), IC6.3 (W), IC6.7 (HOLD), IC6.8 (VCC), IC8.4 (VCC), L3.2, Q4.1 (G), Q5.1 (G), R7.2, R10.2, R14.2, R15.2, R16.2, R27.2, R29.2, R30.2, R31.1, TP5.TP
VDD: C7.1, IC3.1 (IN), IC3.3 (EN), L1.2, L2.2, R21.2, R22.2, R26.2
VSYNC: CAM1.18 (VSYNC), IC4.59 (PB7/DCMI_VSYNC)
XCLK: CAM1.12 (XCLK), IC4.41 (PA8/MCO)

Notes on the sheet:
typ. load 4k7
Sallen-Key LPF, fc=3.38kHz, Q=0.81
SatCam - SSTV Camera Module
(c) 2015-2020 OK2ALP
dummy

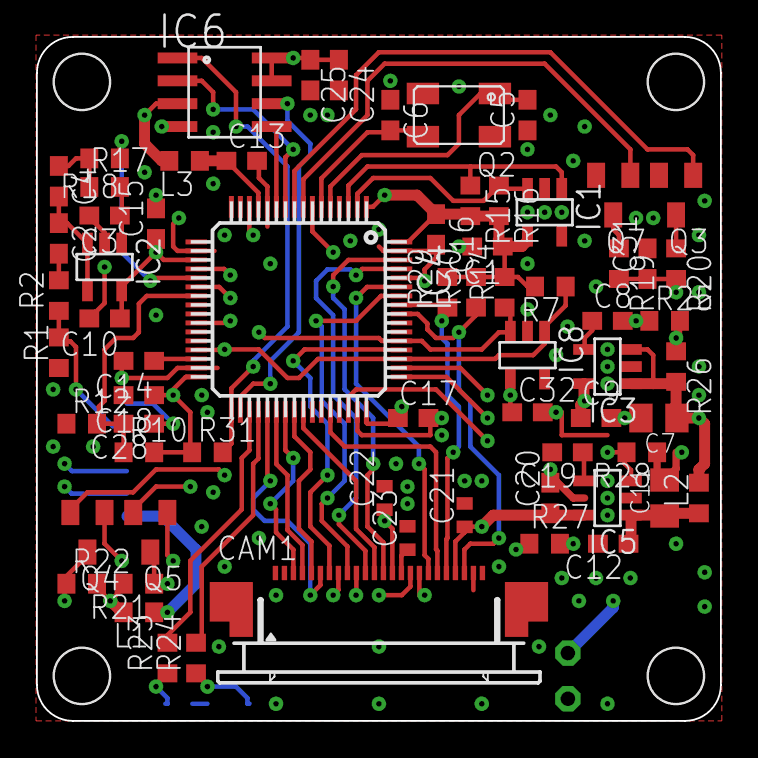
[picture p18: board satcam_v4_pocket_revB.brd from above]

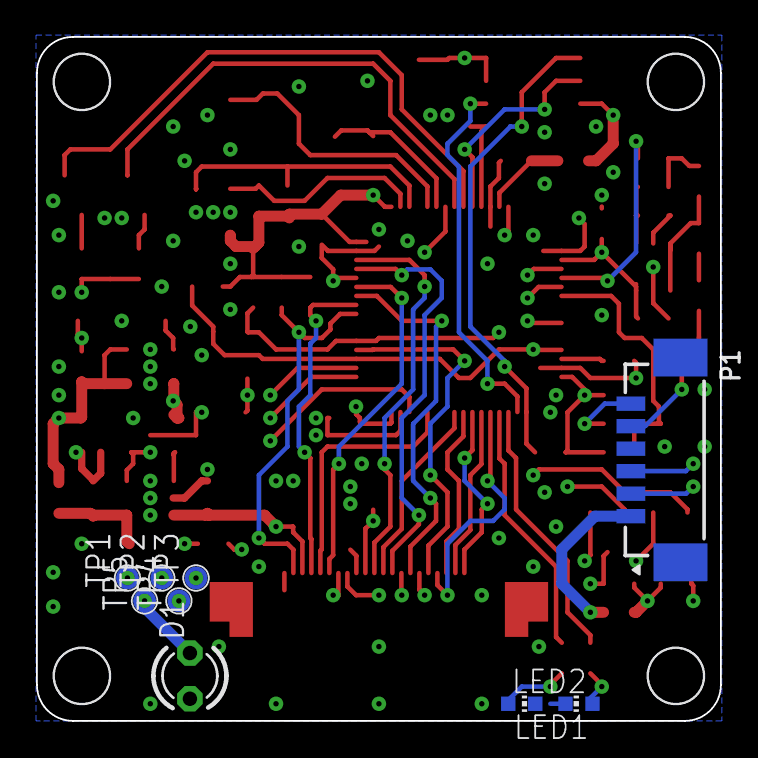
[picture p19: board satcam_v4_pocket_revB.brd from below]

Board: 4 copper layers, 38.0 x 38.0 mm, 80 parts (9 on the bottom side), 60 nets.

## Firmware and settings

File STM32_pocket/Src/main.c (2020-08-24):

/**
  ******************************************************************************
  * File Name          : main.c
  * Description        : Main program body
  ******************************************************************************
  *
  * COPYRIGHT(c) 2020 STMicroelectronics
  *
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
  ******************************************************************************
  */
/* Includes ------------------------------------------------------------------*/
#include "main.h"
#include "stm32f4xx_hal.h"

/* USER CODE BEGIN Includes */
#include "cube.h"

/* USER CODE END Includes */

ADC_HandleTypeDef hadc1;

CRC_HandleTypeDef hcrc;

DAC_HandleTypeDef hdac;
DMA_HandleTypeDef hdma_dac2;

DCMI_HandleTypeDef hdcmi;
DMA_HandleTypeDef hdma_dcmi;

I2C_HandleTypeDef hi2c2;

IWDG_HandleTypeDef hiwdg;

SPI_HandleTypeDef hspi2;
DMA_HandleTypeDef hdma_spi2_rx;
DMA_HandleTypeDef hdma_spi2_tx;

TIM_HandleTypeDef htim6;

/* USER CODE BEGIN PV */
uint8_t i2c_delay_value = 255; // I2C half bit delay derived from HCLK

/* USER CODE END PV */

void SystemClock_Config(void);
void Error_Handler(void);
static void MX_GPIO_Init(void);
static void MX_DMA_Init(void);
static void MX_ADC1_Init(void);
static void MX_CRC_Init(void);
static void MX_DAC_Init(void);
static void MX_DCMI_Init(void);
static void MX_I2C2_Init(void);
static void MX_IWDG_Init(void);
static void MX_TIM6_Init(void);
static void MX_SPI2_Init(void);

/* USER CODE BEGIN PFP */

/* USER CODE END PFP */

/* USER CODE BEGIN 0 */

static void i2c_set_freq(uint32_t hclk)
{
    /* calculate ticks count for half bit delay based on HCLK */
    i2c_delay_value = (hclk / 5) / (SOFT_I2C_SPEED * 2);
    if (i2c_delay_value < 2) i2c_delay_value = 1;
    else i2c_delay_value--;
}

void enable_turbo(bool en)
{
    RCC_OscInitTypeDef RCC_OscInitStruct;
    RCC_ClkInitTypeDef RCC_ClkInitStruct;

    if (en) {
        /* enable HSE and PLL */
        RCC_OscInitStruct.OscillatorType = RCC_OSCILLATORTYPE_HSE;
        RCC_OscInitStruct.HSEState = RCC_HSE_ON;
        RCC_OscInitStruct.PLL.PLLState = RCC_PLL_ON;
        RCC_OscInitStruct.PLL.PLLSource = RCC_PLLSOURCE_HSE;
        RCC_OscInitStruct.PLL.PLLM = 8;
        RCC_OscInitStruct.PLL.PLLN = 160;
        RCC_OscInitStruct.PLL.PLLP = RCC_PLLP_DIV2;
        RCC_OscInitStruct.PLL.PLLQ = 2;
        RCC_OscInitStruct.PLL.PLLR = 7;
        HAL_RCC_OscConfig(&RCC_OscInitStruct);

        /* SYSCLK=80MHz, AHB=HCLK=80MHz, APB1=PCLK1=10MHz, APB2=PCLK2=10MHz, 2WS, prefetch enabled */
        RCC_ClkInitStruct.ClockType = RCC_CLOCKTYPE_HCLK|RCC_CLOCKTYPE_SYSCLK|RCC_CLOCKTYPE_PCLK1|RCC_CLOCKTYPE_PCLK2;
        RCC_ClkInitStruct.SYSCLKSource = RCC_SYSCLKSOURCE_PLLCLK;
        RCC_ClkInitStruct.AHBCLKDivider = RCC_SYSCLK_DIV1;
        RCC_ClkInitStruct.APB1CLKDivider = RCC_HCLK_DIV8;
        RCC_ClkInitStruct.APB2CLKDivider = RCC_HCLK_DIV8;
        HAL_RCC_ClockConfig(&RCC_ClkInitStruct, FLASH_LATENCY_2);
        __HAL_FLASH_PREFETCH_BUFFER_ENABLE();

        /* reconfigure dependent timers, clocks, rates */
        HAL_SYSTICK_Config(HAL_RCC_GetHCLKFreq()/1000);
        htim6.Instance->PSC = (20-1);
        i2c_set_freq(HAL_RCC_GetHCLKFreq());
        hi2c2.Instance->CR2 = (hi2c2.Instance->CR2 & ~I2C_CR2_FREQ) | (10);
    }
    else {
        /* SYSCLK=8MHz, AHB=HCLK=4MHz, APB1=PCLK1=4MHz, APB2=PCLK2=4MHz, 0WS, prefetch disabled */
        RCC_ClkInitStruct.ClockType = RCC_CLOCKTYPE_HCLK|RCC_CLOCKTYPE_SYSCLK|RCC_CLOCKTYPE_PCLK1|RCC_CLOCKTYPE_PCLK2;
        RCC_ClkInitStruct.SYSCLKSource = RCC_SYSCLKSOURCE_HSE;
        RCC_ClkInitStruct.AHBCLKDivider = RCC_SYSCLK_DIV2;
        RCC_ClkInitStruct.APB1CLKDivider = RCC_HCLK_DIV1;
        RCC_ClkInitStruct.APB2CLKDivider = RCC_HCLK_DIV1;
        HAL_RCC_ClockConfig(&RCC_ClkInitStruct, FLASH_LATENCY_0);
        __HAL_FLASH_PREFETCH_BUFFER_DISABLE();

        /* reconfigure dependent timers, clocks, rates */
        HAL_SYSTICK_Config(HAL_RCC_GetHCLKFreq()/1000);
        htim6.Instance->PSC = (4-1);
        i2c_set_freq(HAL_RCC_GetHCLKFreq());
        hi2c2.Instance->CR2 = (hi2c2.Instance->CR2 & ~I2C_CR2_FREQ) | (4);

        /* keep HSE, disable PLL */
        RCC_OscInitStruct.OscillatorType = RCC_OSCILLATORTYPE_HSE;
        RCC_OscInitStruct.HSEState = RCC_HSE_ON;
        RCC_OscInitStruct.PLL.PLLState = RCC_PLL_OFF;
        HAL_RCC_OscConfig(&RCC_OscInitStruct);
    }
}


void HAL_Delay(__IO uint32_t Delay)
{
    uint32_t tickstart = 0;
    tickstart = HAL_GetTick();
    while ((HAL_GetTick() - tickstart) < Delay) {
        /* enter SLEEP mode for next 1ms at most */
        HAL_PWR_EnterSLEEPMode(PWR_MAINREGULATOR_ON, PWR_SLEEPENTRY_WFI);
    }
}


/* USER CODE END 0 */

int main(void)
{

  /* MCU Configuration----------------------------------------------------------*/

  /* Reset of all peripherals, Initializes the Flash interface and the Systick. */
  HAL_Init();

  /* Configure the system clock */
  SystemClock_Config();

  /* Initialize all configured peripherals */
  MX_GPIO_Init();
  MX_DMA_Init();
  MX_ADC1_Init();
  MX_CRC_Init();
  MX_DAC_Init();
  MX_DCMI_Init();
  MX_I2C2_Init();
  MX_IWDG_Init();
  MX_TIM6_Init();
  MX_SPI2_Init();

  /* USER CODE BEGIN 2 */

  enable_turbo(false);
  main_satcam();

  /* USER CODE END 2 */

  /* Infinite loop */
  /* USER CODE BEGIN WHILE */
  while (1)
  {
  /* USER CODE END WHILE */

  /* USER CODE BEGIN 3 */

  }
  /* USER CODE END 3 */

}

/** System Clock Configuration
*/
void SystemClock_Config(void)
{

  RCC_OscInitTypeDef RCC_OscInitStruct;
  RCC_ClkInitTypeDef RCC_ClkInitStruct;

    /**Configure the main internal regulator output voltage
    */
  __HAL_RCC_PWR_CLK_ENABLE();

  __HAL_PWR_VOLTAGESCALING_CONFIG(PWR_REGULATOR_VOLTAGE_SCALE3);

    /**Initializes the CPU, AHB and APB busses clocks
    */
  RCC_OscInitStruct.OscillatorType = RCC_OSCILLATORTYPE_LSI|RCC_OSCILLATORTYPE_HSE;
  RCC_OscInitStruct.HSEState = RCC_HSE_ON;
  RCC_OscInitStruct.LSIState = RCC_LSI_ON;
  RCC_OscInitStruct.PLL.PLLState = RCC_PLL_NONE;
  if (HAL_RCC_OscConfig(&RCC_OscInitStruct) != HAL_OK)
  {
    Error_Handler();
  }

    /**Initializes the CPU, AHB and APB busses clocks
    */
  RCC_ClkInitStruct.ClockType = RCC_CLOCKTYPE_HCLK|RCC_CLOCKTYPE_SYSCLK
                              |RCC_CLOCKTYPE_PCLK1|RCC_CLOCKTYPE_PCLK2;
  RCC_ClkInitStruct.SYSCLKSource = RCC_SYSCLKSOURCE_HSE;
  RCC_ClkInitStruct.AHBCLKDivider = RCC_SYSCLK_DIV2;
  RCC_ClkInitStruct.APB1CLKDivider = RCC_HCLK_DIV1;
  RCC_ClkInitStruct.APB2CLKDivider = RCC_HCLK_DIV1;

  if (HAL_RCC_ClockConfig(&RCC_ClkInitStruct, FLASH_LATENCY_0) != HAL_OK)
  {
    Error_Handler();
  }

    /**Configure the Systick interrupt time
    */
  HAL_SYSTICK_Config(HAL_RCC_GetHCLKFreq()/1000);

    /**Configure the Systick
    */
  HAL_SYSTICK_CLKSourceConfig(SYSTICK_CLKSOURCE_HCLK);

  /* SysTick_IRQn interrupt configuration */
  HAL_NVIC_SetPriority(SysTick_IRQn, 0, 0);
}

/* ADC1 init function */
static void MX_ADC1_Init(void)
{

  ADC_ChannelConfTypeDef sConfig;

    /**Configure the global features of the ADC (Clock, Resolution, Data Alignment and number of conversion)
    */
  hadc1.Instance = ADC1;
  hadc1.Init.ClockPrescaler = ADC_CLOCK_SYNC_PCLK_DIV2;
  hadc1.Init.Resolution = ADC_RESOLUTION_12B;
  hadc1.Init.ScanConvMode = DISABLE;
  hadc1.Init.ContinuousConvMode = ENABLE;
  hadc1.Init.DiscontinuousConvMode = DISABLE;
  hadc1.Init.ExternalTrigConvEdge = ADC_EXTERNALTRIGCONVEDGE_NONE;
  hadc1.Init.DataAlign = ADC_DATAALIGN_RIGHT;
  hadc1.Init.NbrOfConversion = 1;
  hadc1.Init.DMAContinuousRequests = DISABLE;
  hadc1.Init.EOCSelection = ADC_EOC_SEQ_CONV;
  if (HAL_ADC_Init(&hadc1) != HAL_OK)
  {
    Error_Handler();
  }

    /**Configure for the selected ADC regular channel its corresponding rank in the sequencer and its sample time.
    */
  sConfig.Channel = ADC_CHANNEL_0;
  sConfig.Rank = 1;
  sConfig.SamplingTime = ADC_SAMPLETIME_144CYCLES;
  if (HAL_ADC_ConfigChannel(&hadc1, &sConfig) != HAL_OK)
  {
    Error_Handler();
  }

}

/* CRC init function */
static void MX_CRC_Init(void)
{

  hcrc.Instance = CRC;
  if (HAL_CRC_Init(&hcrc) != HAL_OK)
  {
    Error_Handler();
  }

}

/* DAC init function */
static void MX_DAC_Init(void)
{

  DAC_ChannelConfTypeDef sConfig;

    /**DAC Initialization
    */
  hdac.Instance = DAC;
  if (HAL_DAC_Init(&hdac) != HAL_OK)
  {
    Error_Handler();
  }

    /**DAC channel OUT2 config
    */
  sConfig.DAC_Trigger = DAC_TRIGGER_T6_TRGO;
  sConfig.DAC_OutputBuffer = DAC_OUTPUTBUFFER_ENABLE;
  if (HAL_DAC_ConfigChannel(&hdac, &sConfig, DAC_CHANNEL_2) != HAL_OK)
  {
    Error_Handler();
  }

}

/* DCMI init function */
static void MX_DCMI_Init(void)
{

  hdcmi.Instance = DCMI;
  hdcmi.Init.SynchroMode = DCMI_SYNCHRO_HARDWARE;
  hdcmi.Init.PCKPolarity = DCMI_PCKPOLARITY_RISING;
  hdcmi.Init.VSPolarity = DCMI_VSPOLARITY_LOW;
  hdcmi.Init.HSPolarity = DCMI_HSPOLARITY_LOW;
  hdcmi.Init.CaptureRate = DCMI_CR_ALL_FRAME;
  hdcmi.Init.ExtendedDataMode = DCMI_EXTEND_DATA_8B;
  hdcmi.Init.JPEGMode = DCMI_JPEG_ENABLE;
  hdcmi.Init.ByteSelectMode = DCMI_BSM_ALL;
  hdcmi.Init.ByteSelectStart = DCMI_OEBS_ODD;
  hdcmi.Init.LineSelectMode = DCMI_LSM_ALL;
  hdcmi.Init.LineSelectStart = DCMI_OELS_ODD;
  if (HAL_DCMI_Init(&hdcmi) != HAL_OK)
  {
    Error_Handler();
  }

}

/* I2C2 init function */
static void MX_I2C2_Init(void)
{

  hi2c2.Instance = I2C2;
  hi2c2.Init.ClockSpeed = 100000;
  hi2c2.Init.DutyCycle = I2C_DUTYCYCLE_2;
  hi2c2.Init.OwnAddress1 = 120;
  hi2c2.Init.AddressingMode = I2C_ADDRESSINGMODE_7BIT;
  hi2c2.Init.DualAddressMode = I2C_DUALADDRESS_DISABLE;
  hi2c2.Init.OwnAddress2 = 0;
  hi2c2.Init.GeneralCallMode = I2C_GENERALCALL_DISABLE;
  hi2c2.Init.NoStretchMode = I2C_NOSTRETCH_DISABLE;
  if (HAL_I2C_Init(&hi2c2) != HAL_OK)
  {
    Error_Handler();
  }

}

/* IWDG init function */
static void MX_IWDG_Init(void)
{

  hiwdg.Instance = IWDG;
  hiwdg.Init.Prescaler = IWDG_PRESCALER_32;
  hiwdg.Init.Reload = 2000;
  if (HAL_IWDG_Init(&hiwdg) != HAL_OK)
  {
    Error_Handler();
  }

}

/* SPI2 init function */
static void MX_SPI2_Init(void)
{

  hspi2.Instance = SPI2;
  hspi2.Init.Mode = SPI_MODE_MASTER;
  hspi2.Init.Direction = SPI_DIRECTION_2LINES;
  hspi2.Init.DataSize = SPI_DATASIZE_8BIT;
  hspi2.Init.CLKPolarity = SPI_POLARITY_HIGH;
  hspi2.Init.CLKPhase = SPI_PHASE_2EDGE;
  hspi2.Init.NSS = SPI_NSS_SOFT;
  hspi2.Init.BaudRatePrescaler = SPI_BAUDRATEPRESCALER_2;
  hspi2.Init.FirstBit = SPI_FIRSTBIT_MSB;
  hspi2.Init.TIMode = SPI_TIMODE_DISABLE;
  hspi2.Init.CRCCalculation = SPI_CRCCALCULATION_DISABLE;
  hspi2.Init.CRCPolynomial = 10;
  if (HAL_SPI_Init(&hspi2) != HAL_OK)
  {
    Error_Handler();
  }

}

/* TIM6 init function */
static void MX_TIM6_Init(void)
{

  TIM_MasterConfigTypeDef sMasterConfig;

  htim6.Instance = TIM6;
  htim6.Init.Prescaler = 19;
  htim6.Init.CounterMode = TIM_COUNTERMODE_UP;
  htim6.Init.Period = 49;
  if (HAL_TIM_Base_Init(&htim6) != HAL_OK)
  {
    Error_Handler();
  }

  sMasterConfig.MasterOutputTrigger = TIM_TRGO_UPDATE;
  sMasterConfig.MasterSlaveMode = TIM_MASTERSLAVEMODE_DISABLE;
  if (HAL_TIMEx_MasterConfigSynchronization(&htim6, &sMasterConfig) != HAL_OK)
  {
    Error_Handler();
  }

}

/**
  * Enable DMA controller clock
  */
static void MX_DMA_Init(void)
{
  /* DMA controller clock enable */
  __HAL_RCC_DMA1_CLK_ENABLE();
  __HAL_RCC_DMA2_CLK_ENABLE();

  /* DMA interrupt init */
  /* DMA1_Stream3_IRQn interrupt configuration */
  HAL_NVIC_SetPriority(DMA1_Stream3_IRQn, 2, 0);
  HAL_NVIC_EnableIRQ(DMA1_Stream3_IRQn);
  /* DMA1_Stream4_IRQn interrupt configuration */
  HAL_NVIC_SetPriority(DMA1_Stream4_IRQn, 2, 0);
  HAL_NVIC_EnableIRQ(DMA1_Stream4_IRQn);
  /* DMA1_Stream6_IRQn interrupt configuration */
  HAL_NVIC_SetPriority(DMA1_Stream6_IRQn, 1, 0);
  HAL_NVIC_EnableIRQ(DMA1_Stream6_IRQn);
  /* DMA2_Stream1_IRQn interrupt configuration */
  HAL_NVIC_SetPriority(DMA2_Stream1_IRQn, 1, 0);
  HAL_NVIC_EnableIRQ(DMA2_Stream1_IRQn);

}

/** Configure pins as
        * Analog
        * Input
        * Output
        * EVENT_OUT
        * EXTI
        * Free pins are configured automatically as Analog (this feature is enabled through
        * the Code Generation settings)
*/
static void MX_GPIO_Init(void)
{

  GPIO_InitTypeDef GPIO_InitStruct;

  /* GPIO Ports Clock Enable */
  __HAL_RCC_GPIOC_CLK_ENABLE();
  __HAL_RCC_GPIOH_CLK_ENABLE();
  __HAL_RCC_GPIOA_CLK_ENABLE();
  __HAL_RCC_GPIOB_CLK_ENABLE();
  __HAL_RCC_GPIOD_CLK_ENABLE();

  /*Configure GPIO pin Output Level */
  HAL_GPIO_WritePin(GPIOC, EEP_SDA_Pin|EEP_SCL_Pin, GPIO_PIN_SET);

  /*Configure GPIO pin Output Level */
  HAL_GPIO_WritePin(GPIOC, SENS_RNG1_Pin|SENS_RNG2_Pin, GPIO_PIN_RESET);

  /*Configure GPIO pin Output Level */
  HAL_GPIO_WritePin(GPIOB, SPI2_NSS_Pin|LED_G_Pin|LED_R_Pin, GPIO_PIN_RESET);

  /*Configure GPIO pin Output Level */
  HAL_GPIO_WritePin(GPIOA, XCLK_Pin|CAM_RST_Pin|CAM_ENB_Pin, GPIO_PIN_RESET);

  /*Configure GPIO pin Output Level */
  HAL_GPIO_WritePin(GPIOB, CAM_SDA_Pin|CAM_SCL_Pin, GPIO_PIN_SET);

  /*Configure GPIO pins : EEP_SDA_Pin EEP_SCL_Pin */
  GPIO_InitStruct.Pin = EEP_SDA_Pin|EEP_SCL_Pin;
  GPIO_InitStruct.Mode = GPIO_MODE_OUTPUT_OD;
  GPIO_InitStruct.Pull = GPIO_PULLUP;
  GPIO_InitStruct.Speed = GPIO_SPEED_FREQ_LOW;
  HAL_GPIO_Init(GPIOC, &GPIO_InitStruct);

  /*Configure GPIO pins : PC15 PC4 PC5 I2C2_SCL_dummy_Pin */
  GPIO_InitStruct.Pin = GPIO_PIN_15|GPIO_PIN_4|GPIO_PIN_5|I2C2_SCL_dummy_Pin;
  GPIO_InitStruct.Mode = GPIO_MODE_ANALOG;
  GPIO_InitStruct.Pull = GPIO_NOPULL;
  HAL_GPIO_Init(GPIOC, &GPIO_InitStruct);

  /*Configure GPIO pins : SENS_RNG1_Pin SENS_RNG2_Pin */
  GPIO_InitStruct.Pin = SENS_RNG1_Pin|SENS_RNG2_Pin;
  GPIO_InitStruct.Mode = GPIO_MODE_OUTPUT_PP;
  GPIO_InitStruct.Pull = GPIO_NOPULL;
  GPIO_InitStruct.Speed = GPIO_SPEED_FREQ_LOW;
  HAL_GPIO_Init(GPIOC, &GPIO_InitStruct);

  /*Configure GPIO pins : PA1 PA2 PA3 PA9
                           PA10 ADC1_IN8_dummy_Pin */
  GPIO_InitStruct.Pin = GPIO_PIN_1|GPIO_PIN_2|GPIO_PIN_3|GPIO_PIN_9
                          |GPIO_PIN_10|ADC1_IN8_dummy_Pin;
  GPIO_InitStruct.Mode = GPIO_MODE_ANALOG;
  GPIO_InitStruct.Pull = GPIO_NOPULL;
  HAL_GPIO_Init(GPIOA, &GPIO_InitStruct);

  /*Configure GPIO pins : PB1 PB2 */
  GPIO_InitStruct.Pin = GPIO_PIN_1|GPIO_PIN_2;
  GPIO_InitStruct.Mode = GPIO_MODE_ANALOG;
  GPIO_InitStruct.Pull = GPIO_NOPULL;
  HAL_GPIO_Init(GPIOB, &GPIO_InitStruct);

  /*Configure GPIO pin : SPI2_NSS_Pin */
  GPIO_InitStruct.Pin = SPI2_NSS_Pin;
  GPIO_InitStruct.Mode = GPIO_MODE_OUTPUT_PP;
  GPIO_InitStruct.Pull = GPIO_NOPULL;
  GPIO_InitStruct.Speed = GPIO_SPEED_FREQ_VERY_HIGH;
  HAL_GPIO_Init(SPI2_NSS_GPIO_Port, &GPIO_InitStruct);

  /*Configure GPIO pins : LED_G_Pin LED_R_Pin */
  GPIO_InitStruct.Pin = LED_G_Pin|LED_R_Pin;
  GPIO_InitStruct.Mode = GPIO_MODE_OUTPUT_PP;
  GPIO_InitStruct.Pull = GPIO_NOPULL;
  GPIO_InitStruct.Speed = GPIO_SPEED_FREQ_LOW;
  HAL_GPIO_Init(GPIOB, &GPIO_InitStruct);

  /*Configure GPIO pin : XCLK_Pin */
  GPIO_InitStruct.Pin = XCLK_Pin;
  GPIO_InitStruct.Mode = GPIO_MODE_OUTPUT_PP;
  GPIO_InitStruct.Pull = GPIO_NOPULL;
  GPIO_InitStruct.Speed = GPIO_SPEED_FREQ_VERY_HIGH;
  HAL_GPIO_Init(XCLK_GPIO_Port, &GPIO_InitStruct);

  /*Configure GPIO pins : CAM_RST_Pin CAM_ENB_Pin */
  GPIO_InitStruct.Pin = CAM_RST_Pin|CAM_ENB_Pin;
  GPIO_InitStruct.Mode = GPIO_MODE_OUTPUT_PP;
  GPIO_InitStruct.Pull = GPIO_NOPULL;
  GPIO_InitStruct.Speed = GPIO_SPEED_FREQ_LOW;
  HAL_GPIO_Init(GPIOA, &GPIO_InitStruct);

  /*Configure GPIO pin : PD2 */
  GPIO_InitStruct.Pin = GPIO_PIN_2;
  GPIO_InitStruct.Mode = GPIO_MODE_ANALOG;
  GPIO_InitStruct.Pull = GPIO_NOPULL;
  HAL_GPIO_Init(GPIOD, &GPIO_InitStruct);

  /*Configure GPIO pins : CAM_SDA_Pin CAM_SCL_Pin */
  GPIO_InitStruct.Pin = CAM_SDA_Pin|CAM_SCL_Pin;
  GPIO_InitStruct.Mode = GPIO_MODE_OUTPUT_OD;
  GPIO_InitStruct.Pull = GPIO_PULLUP;
  GPIO_InitStruct.Speed = GPIO_SPEED_FREQ_HIGH;
  HAL_GPIO_Init(GPIOB, &GPIO_InitStruct);

}

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


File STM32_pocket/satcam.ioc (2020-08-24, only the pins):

Mcu.UserName=STM32F446RETx
PA0-WKUP.Signal=ADCx_IN0
PA11.GPIO_Label=CAM_RST
PA11.Signal=GPIO_Output
PA12.GPIO_Label=ADC1_IN8_dummy
PA12.Signal=GPIO_Analog
PA13.Signal=SYS_JTMS-SWDIO
PA14.Signal=SYS_JTCK-SWCLK
PA15.GPIO_Label=CAM_ENB
PA15.Signal=GPIO_Output
PA4.Signal=DCMI_HSYNC
PA5.Signal=COMP_DAC2_group
PA6.Signal=DCMI_PIXCLK
PA7.Signal=ADCx_IN7
PA8.GPIO_Label=XCLK
PA8.Signal=GPIO_Output
PB0.Signal=ADCx_IN8
PB10.Signal=I2C2_SCL
PB12.GPIO_Label=SPI2_NSS
PB12.Signal=GPIO_Output
PB13.Signal=SPI2_SCK
PB14.GPIO_Label=LED_G
PB14.Signal=GPIO_Output
PB15.GPIO_Label=LED_R
PB15.Signal=GPIO_Output
PB3.Signal=SYS_JTDO-SWO
PB4.GPIO_Label=CAM_SDA
PB4.Signal=GPIO_Output
PB5.GPIO_Label=CAM_SCL
PB5.Signal=GPIO_Output
PB6.Signal=DCMI_D5
PB7.Signal=DCMI_VSYNC
PB8.Signal=DCMI_D6
PB9.Signal=DCMI_D7
PC0.GPIO_Label=SENS_RNG1
PC0.Signal=GPIO_Output
PC1.GPIO_Label=SENS_RNG2
PC1.Signal=GPIO_Output
PC10.GPIO_Label=I2C2_SCL_dummy
PC10.Signal=GPIO_Analog
PC11.Signal=DCMI_D4
PC12.Signal=I2C2_SDA
PC13.GPIO_Label=EEP_SDA
PC13.Signal=GPIO_Output
PC14-OSC32_IN.GPIO_Label=EEP_SCL
PC14-OSC32_IN.Signal=GPIO_Output
PC2.Signal=SPI2_MISO
PC3.Signal=SPI2_MOSI
PC6.Signal=DCMI_D0
PC7.Signal=DCMI_D1
PC8.Signal=DCMI_D2
PC9.Signal=DCMI_D3
PH0-OSC_IN.Signal=RCC_OSC_IN
PH1-OSC_OUT.Signal=RCC_OSC_OUT

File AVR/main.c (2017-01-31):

/*************************************************************************
 *
 * PSK Transponder Module for PSAT-2
 * Copyright (c) 2014-2017 OK2ALP, OK2PNQ, OK2CPV
 * Dept. of Radio Electronics, Brno University of Technology
 *
 * This work is licensed under the terms of the MIT license
 *
 *************************************************************************/

#include <stdio.h>
#include <stdlib.h>
#include <string.h>
#include <ctype.h>
#include <avr/io.h>
#include <avr/interrupt.h>
#include <avr/wdt.h>
#include <avr/eeprom.h>
#include <avr/pgmspace.h>
#include <avr/signature.h>
#include <util/delay.h>
#include "common.h"
#include "i2cmaster.h"
#include "bpsk.h"
#include "adf.h"
#include "meas.h"
#include "eeprom.h"
#include "uart.h"

FUSES = {
    .low = (FUSE_CKSEL3), // full-swing XTAL, 16k+65ms
    .high = (FUSE_SPIEN & FUSE_EESAVE), // preserve EEPROM
    .extended = (FUSE_BODLEVEL1), // BOD at 2.7V
};

/*----------------------------------------------------------------------------------------------------------------*/

volatile uint32_t ClockTimer = 0;


static CONFIG_STRUCT eeprom EEMEM = {
    .MaxMode = MODE_A,
    .PeriodsRX = { PER_RX_D_DEF, PER_RX_C_DEF, PER_RX_B_DEF, PER_RX_A_DEF }, // D to A
    .ProlongTX = { 0, PROL_TX_C_DEF, PROL_TX_B_DEF, PROL_TX_A_DEF }, // D to A
    .THRvoltage = THRV_DEF,
    .PSKdiv = 4,
    .TunerC = TUNER_C_DEF,
    .TunerL = TUNER_L_DEF,
    .SSTVen = 1,
};
CONFIG_STRUCT config;
volatile STATUS_STRUCT status;

/*----------------------------------------------------------------------------------------------------------------*/

void early_wdt_handler(void) __attribute__ ((naked,section(".init3")));
void early_wdt_handler(void)
{
    MCUSR = 0;
    wdt_enable(WDTO_4S);
}


static void TX_ON(void)
{
    if (status.TX) return;
    set_TXPWR(1); // PA on
    _delay_ms(2);
    TX_Enable(); // ADF load regs
    status.TX = true;
    _delay_ms(100);
    SupervisorTask();
    BPSK_SigStart();
    BPSK_SendChar('\f');
}


static void TX_OFF(void)
{
    if (!status.TX) return;
    BPSK_SigStop();
    TX_Disable(); // ADF disable
    set_TXPWR(0); // PA off
    status.TX = false;
}


static void RX_ON(void)
{

    if (status.RX) return;
    set_RXPWR(1); // RX on
    _delay_ms(1);
    status.RX = true;
}


static void RX_OFF(void)
{
    if (!status.RX) return;
    status.RX = false;
    set_RXPWR(0); // RX off
}


static void TunerUpdate(void)
{
    DAC_Write(0, config.TunerC); // channel A - capacitance
    DAC_Write(1, (config.TunerL & 0x01) ? 4095 : 0); // channel B - inductor 1 on/off
    DAC_Write(2, (config.TunerL & 0x02) ? 4095 : 0); // channel C - inductor 2 on/off
    DAC_Write(3, 0); // channel D - unused
}


static void SetMode(uint8_t req_mode)
{
    // check MaxMode in A..D
    if (config.MaxMode > MODE_A) config.MaxMode = MODE_A;

    if (config.MaxMode >= req_mode) {
        // requested mode is allowed, set to requested
        status.Mode = req_mode;
    } else {
        // requested mode over MaxMode, set to MaxMode
        status.Mode = config.MaxMode;
    }

    if (status.Mode == MODE_D) {
        // clear counters for mode D
        status.PeriodsSSTV_noRX = 0;
        status.PeriodsSSTV_keepRX = 0;
        status.PeriodsTX = 0;
    }
}


static void SaveValidatedConfig(void)
{
    // current mode validation
    SetMode(status.Mode);

    // check voltage threshold range, PSK divider in [2,4]
    if ((config.THRvoltage < (THRV_MIN - THRV_STEP)) || (config.THRvoltage > THRV_MAX)) config.THRvoltage = THRV_DEF;
    if (config.PSKdiv != 2 && config.PSKdiv != 4) config.PSKdiv = 4;

    // check number of RX enabled periods in 1..6
    if (config.PeriodsRX[MODE_A] < 1 || config.PeriodsRX[MODE_A] > 6) config.PeriodsRX[MODE_A] = 1;
    if (config.PeriodsRX[MODE_B] < 1 || config.PeriodsRX[MODE_B] > 6) config.PeriodsRX[MODE_B] = 1;
    if (config.PeriodsRX[MODE_C] < 1 || config.PeriodsRX[MODE_C] > 6) config.PeriodsRX[MODE_C] = 1;
    if (config.PeriodsRX[MODE_D] < 1 || config.PeriodsRX[MODE_D] > 6) config.PeriodsRX[MODE_D] = 1;

    // check number of TX prolognation periods in 0..5
    if (config.ProlongTX[MODE_A] > 5) config.ProlongTX[MODE_A] = 0;
    if (config.ProlongTX[MODE_B] > 5) config.ProlongTX[MODE_B] = 0;
    if (config.ProlongTX[MODE_C] > 5) config.ProlongTX[MODE_C] = 0;
    config.ProlongTX[MODE_D] = 0;

    // check antenna tuner values
    if (config.TunerC > 4095) config.TunerC = 4095;
    if (config.TunerL > 0x03) config.TunerL = 0x03;

    // store changed settings to AVR EEPROM
    eeprom_update_block(&config, &eeprom, sizeof(eeprom));
}




void uart_process_char(char c)
{
    switch (c) {
        case PSK_CMD_TX_NO_RX:
            if (status.Mode != MODE_D && status.SunWire) {
                // modes A,B,C - start TX, disable RX, set max number of SSTV periods
                status.PeriodsSSTV_noRX = MAX_SSTV_PERIODS;
                RX_OFF();
                TX_ON();
                uart_putc(PSK_RSP_ACK);
            } else {
                // deny in mode D
                uart_putc(PSK_RSP_DENIED);
            }
            break;
        case PSK_CMD_TX_KEEP_RX:
            if (status.Mode != MODE_D && status.SunWire) {
                // modes A,B,C - start TX, set max number of SSTV periods
                status.PeriodsSSTV_keepRX = MAX_SSTV_PERIODS;
                TX_ON();
                uart_putc(PSK_RSP_ACK);
            } else if (status.TX) {
                // mode D - acknowledge if TX is currently on
                uart_putc(PSK_RSP_ACK);
            } else {
                // otherwise deny in mode D
                uart_putc(PSK_RSP_DENIED);
            }
            break;
        case PSK_CMD_TX_IDLE:
            if (status.TX) {
                // acknowledge if TX is currently on
                uart_putc(PSK_RSP_ACK);
            } else {
                // otherwise deny
                uart_putc(PSK_RSP_DENIED);
            }
            break;
        case PSK_CMD_STOP_TX:
            // clear number of SSTV periods
            status.PeriodsSSTV_noRX = 0;
            status.PeriodsSSTV_keepRX = 0;
            break;
    }
}


void SunWireUpdate(void)
{
    bool sunwire_new = get_SUNWIRE();
    static bool sunwire_old = false;
    static uint32_t last_sun = 0;

    // check sun wire
    bool sun_fall = sunwire_old && !sunwire_new;
    bool sun_rise = !sunwire_old && sunwire_new;
    bool timeout = last_sun && (ClockTimer - last_sun > TSUNWIRE);

    if (sun_fall) {
        // falling edge
        status.SunWire = false;
        last_sun = ClockTimer;
    }
    else if (sun_rise || timeout) {
        // rising edge
        status.SunWire = true;
        last_sun = 0;
    }
    sunwire_old = sunwire_new;
}
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

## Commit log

2017-01-31 SVN revision 984
    [ov2640_module_v2.brd, ov2640_module_v2.sch, satcam_v2.brd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]
2019-09-16 SVN revision 1130
    [satcam_v3_mini.brd, satcam_v3_mini.sch]
2019-11-01 SVN revision 1158
    [satcam_v3_mini.brd, satcam_v3_mini.sch]
2020-01-27 SVN revision 1192
    [satcam_v3_mini.brd, satcam_v3_mini.sch]
2020-08-24 SVN revision 1250
    [i2c_ctrl.cfg, satcam_v4_pocket_revB.brd, satcam_v4_pocket_revB.sch]

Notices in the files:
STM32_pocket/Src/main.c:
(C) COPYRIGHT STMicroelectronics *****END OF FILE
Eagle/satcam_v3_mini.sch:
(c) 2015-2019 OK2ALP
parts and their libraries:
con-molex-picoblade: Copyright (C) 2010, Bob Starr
